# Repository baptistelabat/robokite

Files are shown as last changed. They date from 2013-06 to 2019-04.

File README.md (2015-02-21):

robokite
========

The robokite project aims to provide an open source platform to control kites.

This project started in 2013. It aims to provide tools or interface between existing tools to control big kites in a few years. Applications vary from ship propulsion to Airborne Wind Energy, through arstistic control.

Watch the video below to understand the current state of the project or have a look to the project blog http://robokite.blogspot.fr/

Joystick kite control (https://www.youtube.com/watch?v=0MbRyefYqPs&index=1&list=UUa67hFWRqXyehBhyk3YfBnA)

The first step is to design a simple kite control system:

* inexpensive
* adaptable to any small kite
* based on a community of users 

The solutions which are tested:
    
* Mobile phone (webcam, accelerometer, magnetometer, and gyro if available) for kite position sensing from ground
* Wifi streaming to a computer (might be raspberry) and processing with python (simplecv) in a first step
* Processing with OpenCV for Android then streaming to reduce latency, in a second step
* IMU embedded on kite with radio link to ground
* A webserver (python tornado)
* A browser with HTML5 as interface (websocket for real time, slider for controls, webgl for visualization, graphs, etc)
* A common gamepad joystick to send orders
* Serial NMEA or mavlink communication
* Arduino as a DAC (Digital-Analog Converter)
* Sabertooth as motor control card (to be replaced by open hardware)
* Recycled cordless drill as motor, but scalable.

Installation
------------

Please use the following command to get the code (you need to have git installed):

    git clone https://github.com/baptistelabat/robokite.git

This will create a repertory robokite containing the source code.

The following command will download the depencies (tests on ubuntu 14.04, work in progress):

    cd robokite
    chmod 777 install.sh
    ./install.sh

Feature status
--------------

Currently, the project enables to control the kite with some motors controlled by a joystick.

Documentation
--------------

The project hosts the documentation on the [wiki] (https://github.com/baptistelabat/robokite/wiki). Please use the following command to get the documentation offline:

    git clone https://github.com/baptistelabat/robokite.wiki.git

To get more up to date news, you can follow the [robokite blog](http://robokite.blogspot.fr/) 

Mailing list
------------

There is a public [mailing list](https://groups.google.com/group/robokite)
for Robokite users and developers.

Development
-----------

We are currently looking for some beta testers and developers.

Please mail nautilabs@gmail.com to be involved. 

Acknowledgments
------------

The robokite project is based on many open source or open hardware parts and was possible thanks to the support of several individuals and structures.

See [acknowlegement page in wiki] (https://github.com/baptistelabat/robokite/wiki/Acknowledgment).

License
-------

Robokite is covered by the MIT license, see the accompanying file LICENSE.md for details.

This repository contains additional code that may be covered by other licenses.

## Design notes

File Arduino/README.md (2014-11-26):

Arduino sketches
========

This directory host the arduino sketches.
Some are just some tests to checks sensors, actuators or communication links.

Simple: load this program on an arduino connected to a Sabertooth card controlling motors.
It receives order via NMEA messages on serial port. 
See motorJoy.py to generate orders from an USB joystick.

MPU9150_AHRS: this is the program to load on the arduino board connected to the IMU onboard kite.
It is making the data fusion of accelerometer, gyro and magnetometer
The software was found to work with MPU6050 alone and with MPU9050

Tests program
ArduinoMAVLink: this is a test to send fake attitude and gps data from arduino to ground control station with MAVLink

Electronic_rule: this is the program used to read measurement from the diy linear encoder.

Other sketches are obsolete

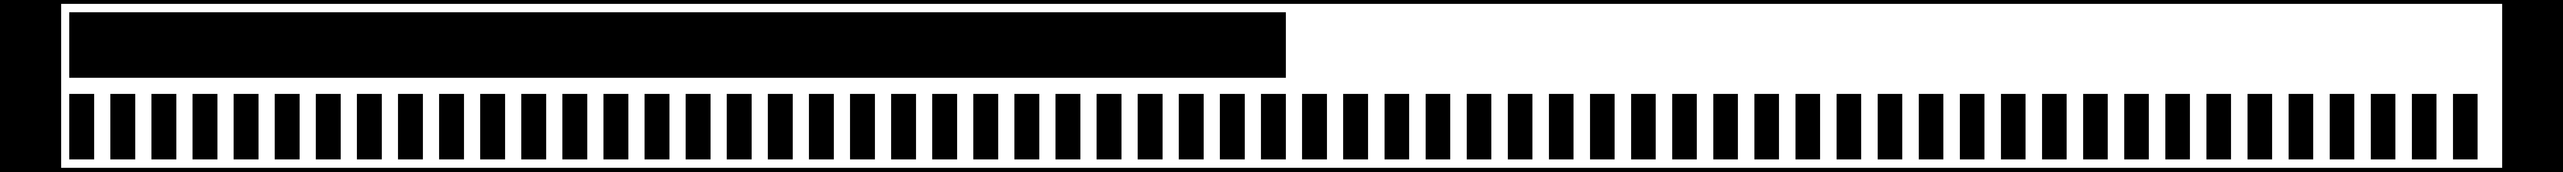
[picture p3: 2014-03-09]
Hardware/electronic_rule/sticker.png

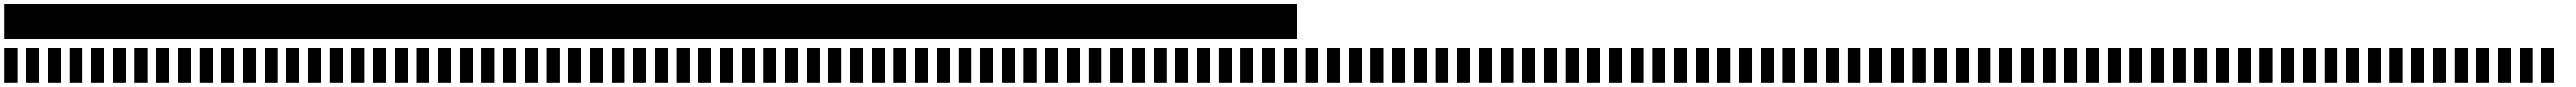
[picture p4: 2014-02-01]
Hardware/electronic_rule/stickerA3.png

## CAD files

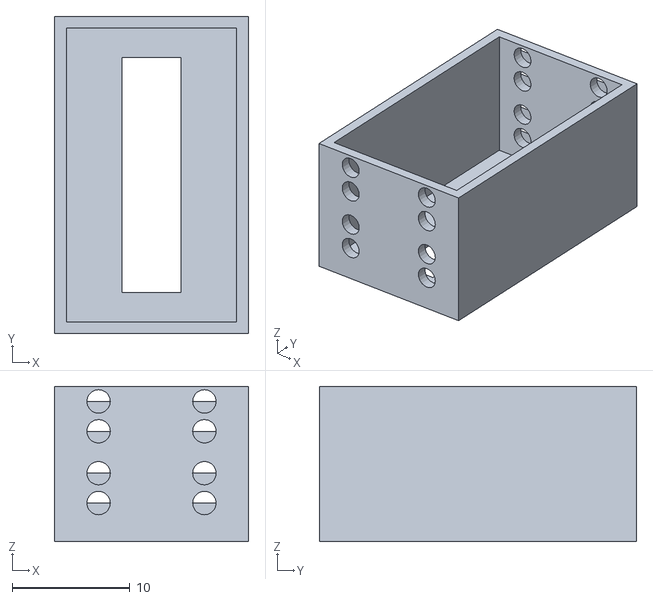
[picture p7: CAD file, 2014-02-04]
Hardware/electronic_rule/slider.stl
16.5 x 27.0 x 13.2

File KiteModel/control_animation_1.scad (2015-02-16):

distance_between_fixed_pulleys = 30;
distance_between_lines = 30;
control_length_left = 20 + 20*sin($t*360);
control_length_right = 20 + 20*sin($t*360*2);
L=300;


// Left line
hull()
{
translate([ -distance_between_lines,0,0]) sphere(r=1);
translate([ -control_length_left -distance_between_lines, distance_between_fixed_pulleys/2., 0]) sphere(r=1);
};
hull()
{
translate([ -control_length_left -distance_between_lines, distance_between_fixed_pulleys/2., 0]) sphere(r=1);
translate([ -distance_between_lines, distance_between_fixed_pulleys, 0]) sphere(r=1);
};
hull()
{
translate([ -distance_between_lines, distance_between_fixed_pulleys, 0]) sphere(r=1);
translate([ -distance_between_lines, distance_between_fixed_pulleys + 300 -2*sqrt(pow(distance_between_fixed_pulleys/2., 2)+ pow(control_length_left, 2)) , 0]) sphere(r=1);
};

// Central line
hull()
{
translate([ -0*distance_between_lines,0,0]) sphere(r=1);
translate([ -0*distance_between_lines, distance_between_fixed_pulleys, 0]) sphere(r=1);
};
hull()
{
translate([ -0*distance_between_lines, distance_between_fixed_pulleys, 0]) sphere(r=1);
translate([ -0*distance_between_lines, distance_between_fixed_pulleys + L -2*sqrt(pow(distance_between_fixed_pulleys/2., 2)) , 0]) sphere(r=1);
};

// Right line
hull()
{
translate([ distance_between_lines,0,0]) sphere(r=1);
translate([ control_length_right +distance_between_lines, distance_between_fixed_pulleys/2., 0]) sphere(r=1);
};
hull()
{
translate([ control_length_right +distance_between_lines, distance_between_fixed_pulleys/2., 0]) sphere(r=1);
translate([ distance_between_lines, distance_between_fixed_pulleys, 0]) sphere(r=1);
};
hull()
{
translate([ distance_between_lines, distance_between_fixed_pulleys, 0]) sphere(r=1);
translate([ distance_between_lines, distance_between_fixed_pulleys + 300 -2*sqrt(pow(distance_between_fixed_pulleys/2., 2)+ pow(control_length_right, 2)) , 0]) sphere(r=1);
};

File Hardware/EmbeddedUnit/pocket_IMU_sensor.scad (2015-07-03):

thickness = 2;
width=85;
length=133-30;
nano_length_max=43.6;
nano_length_min = 37.1;
nano_width_max = 22.7;
nano_internal_width = 9;
nano_thickness=7;
9V_width=26.2;
9V_length=45;
transmitter_width = 30;
transmitter_length= 45;
IMU_screw_spacing_width = 12.1;
IMU_screw_spacing_length = 16.3;
corner_radius=5;

module support()
{
	difference()
	{
		minkowski(){
		translate([0,-15,0]) cube(size=[width-2*corner_radius,length-2*corner_radius,thickness/3.], center=true);
		cylinder(h=thickness/3., r=corner_radius);
}
		translate([10,12,0]) difference(){
			cube(size=[nano_width_max,nano_length_min,2*thickness], center=true);
		 	cube(size=[nano_internal_width,nano_length_min,2*thickness], center=true);
	}
		translate([-23,8,0]) cube(size=[9V_width,9V_length,2*thickness], center=true);
		//translate([10,-45,0]) cube(size=[transmitter_length,transmitter_width,2*thickness], center=true);
	translate([0,-60,0]) cube(size=[12,3,2*thickness], center=true);
	translate([0,-60 +transmitter_width ,0]) cube(size=[12,3,2*thickness], center=true);
	
	
	// Holes to screw drotek IMU board	
		translate([-30, -50,0]) cylinder(r=0.3, h=2*thickness, center=true);
		translate([-30+IMU_screw_spacing_length, -50+IMU_screw_spacing_width,0]) cylinder(r=0.3, h=2*thickness, center=true);
		translate([-30+IMU_screw_spacing_length, -50,0]) cylinder(r=0.3, h=2*thickness, center=true);
	}
}
projection() support();

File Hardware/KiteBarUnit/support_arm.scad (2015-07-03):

use <compass.scad>
use <arduino_footprint.scad>
use <battery_footprint.scad>


module support_arm()
{
	thickness = 5;
	
	difference()
	{
		union()
		{
			arm();
			minkowski()
			{
				cylinder(r=5, h=thickness/3.0);
				translate([20,0,0]) cube(size=[50,150,thickness/3.0], center=true);
			}		
		}
		translate([20,-45,0]) nano_connector_footprint(2*thickness);
		translate([20,5,0]) 9V_battery();
		translate([0,5,0]) cube(size=[3,12,2*thickness], center=true);
		translate([40,5,0]) cube(size=[3,12,2*thickness], center=true);
		translate([0,-45,0]) cube(size=[3,12,2*thickness], center=true);
		translate([40,-45,0]) cube(size=[3,12,2*thickness], center=true);
	}
}
projection() support_arm();

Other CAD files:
Hardware/RingEncoder/ring_encoder.scad
Hardware/GroundStation/ground_station.scad
Hardware/KiteBarUnit/bar_mount_reduced.scad
Hardware/KiteBarUnit/compass.scad
Hardware/KiteBarUnit/gimbal_connection.scad
Hardware/KiteBarUnit/line_support.scad
Hardware/KiteBarUnit/potentiometer_support.scad
Hardware/KiteBarUnit/ring.scad
Hardware/Obsolete/MobileSupport/mobile_support.scad
Hardware/Obsolete/bar_mount.scad
Hardware/Obsolete/embedded_support.scad
Hardware/Obsolete/line_tension_measurement support.scad
Hardware/Obsolete/tender.scad
Hardware/arduino_footprint.scad
Hardware/bar_mount.scad
Hardware/battery_footprint.scad
Hardware/electronic_rule/slider.scad
Hardware/embedded_support.scad
Hardware/handle.scad
Hardware/line_tension_measurement support.scad
Hardware/mobile_support.scad
Hardware/tender.scad
kite.scad

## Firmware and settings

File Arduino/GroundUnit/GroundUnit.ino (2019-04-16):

// Copyright (c) 2013 Nautilabs
// https://github.com/baptistelabat/robokite

// This file used SoftwareSerial example (Copyright (c) 2012 Dimension Engineering LLC)
// for Sabertooth http://www.dimensionengineering.com/software/SabertoothSimplifiedArduinoLibrary/html/index.html
// See license.txt in the Sabertooth arduino library for license details.
//
// The Sabertooth selector 1 3 5 6 have to be on on.

// Includes
#include <SoftwareSerial.h> 
#include <SabertoothSimplified.h> // From http://www.dimensionengineering.com/software/SabertoothArduinoLibraries.zip
#include <TinyGPS++.h>    // From https://github.com/mikalhart/TinyGPSPlus
#include <PID_v1.h>       // From https://github.com/br3ttb/Arduino-PID-Library/tree/master/PID_v1
#include <SPI.h> // Not actualy used but needed to compile
#include <MavlinkForArduino.h>

// Port definition
#define      TX_PIN 8 // Plug to Sabertooth RX
#define      RX_PIN 10 // Do not plug
#define RF_DATA_PIN 11
#define     LED_PIN 13 // Built-in led


// String management
String inputString = "";         // a string to hold incoming data
boolean stringComplete = false;  // whether the string is complete

// Sabertooth connection
// Note: NOT_A_PIN (0) was previously used for RX which is not used, but this was causing problems
SoftwareSerial SWSerial(RX_PIN, TX_PIN); // RX, TX. RX on no pin (unused), TX on pin 8 (to S1).
SabertoothSimplified ST(SWSerial); // Use SWSerial as the serial port.
int power1, power2;

// NMEA protocol for robust messages
TinyGPSPlus nmea;
// O stands for Opensource, R for Robokite
// The index is the place of the field in the NMEA message
TinyGPSCustom feedback_request      (nmea, "ORFBR", 1);  // Feedback request. The feedback are normalized between 0 and 1023
// The orders are normalized between -127 and 127
TinyGPSCustom pwm1     (nmea, "ORPW1", 1);  // Dimentionless voltage setpoint (Pulse Width Modulation) for Sabertooth output 1
TinyGPSCustom pwm2     (nmea, "ORPW2", 1);  // Dimentionless voltage setpoint (Pulse Width Modulation) for Sabertooth output 2
TinyGPSCustom setpos1  (nmea, "ORSP1", 1);  // Position setpoint for Sabertooth output 1
TinyGPSCustom setpos2  (nmea, "ORSP2", 1);  // Position setpoint for Sabertooth output 2
TinyGPSCustom speedlim1  (nmea, "ORSL1", 1);  // Speed limitation for Sabertooth output 1
TinyGPSCustom speedlim2  (nmea, "ORSL2", 1);  // Speed limitation for Sabertooth output 2
TinyGPSCustom poslim1  (nmea, "ORPL1", 1);  // Position limitation for Sabertooth output 1
TinyGPSCustom poslim2  (nmea, "ORPL2", 1);  // Position limitation for Sabertooth output 2
TinyGPSCustom kpm1 (nmea, "ORKP1", 1); // Proportional coefficient multiplicator
//TinyGPSCustom kim1 (nmea, "ORKI1", 1); // Integral coefficient multiplicator
TinyGPSCustom kdm1 (nmea, "ORKD1", 1); // Derivative coefficient multiplicator
//TinyGPSCustom kpm2 (nmea, "ORKP2", 1); // Proportional coefficient multiplicator
//TinyGPSCustom kim2 (nmea, "ORKI2", 1); // Integral coefficient multiplicator
//TinyGPSCustom kdm2 (nmea, "ORKD2", 1); // Derivative coefficient multiplicator
boolean isFeedbackRequested = false;

uint8_t data[4];  // 2 element array of unsigned 8-bit type, holding Joystick readings



// PID for robust control
// Define Variables we'll be connecting to
double Setpoint1, Input1, Output1;
double Setpoint2, Input2, Output2;
double Input3, Input4, Input5, Input6;
float posSat1 = 1;
float posSat2 = 1;
float speedSat1 = 1;
float speedSat2 = 1;
// Specify the links and initial tuning parameters (Kp, Ki, Kd)
float Kp1 = 1;
float Ki1 = 0.00;
float Kd1 = 0.001;
float Kp2 = 1;
float Ki2 = 0.00;
float Kd2 = 0.001;
PID myPID1(&Input1, &Output1, &Setpoint1, Kp1, Ki1, Kd1, DIRECT);
PID myPID2(&Input2, &Output2, &Setpoint2, Kp2, Ki2, Kd2, DIRECT);


#define ORDER_RATE_ms 100
long last_order_ms = 0;
long last_simu_ms = 0;
int dt_ms = 0;

boolean SIL = false; // Use Software in the Loop simulation

/* HX711 part */
#include "HX711.h"

#define HX711_DOUT  12 // or DAT
#define HX711_CLK   11
#define HX711_GND   13

#define OFFSET -797000 // From raw value when no load
#define SCALE  37.0  // From calibration
HX711 scale;
long raw_value;
void setup()
{
  setupHX711();
  pinMode(LED_PIN, OUTPUT); 
  
  // Initialize software serial communication with Sabertooth 
  SWSerial.begin(9600);
  
  // Initialize serial communications with computer
  Serial.begin(115200);
  
  // Reserve bytes for the inputString:
  inputString.reserve(200);
  
  // Initialize input and setpoint
  Input1 = 0;
  Input2 = 0;
  Input3 = 0;

  Setpoint1 = 0;
  Setpoint2 = 0;
  
  // Turn the PID on
  myPID1.SetMode(MANUAL);
  myPID2.SetMode(MANUAL);
  // Saturate the output to the maximum range (values are normalized between -1 and 1)
  myPID1.SetOutputLimits(-1, 1);
  myPID2.SetOutputLimits(-1, 1);
  
  for (int i=0;i<4;i++)
  {
    data[i] = 127;
  }
  
  last_simu_ms = millis();
}

void setupHX711() {
  // Ground connection
  scale.begin(HX711_DOUT, HX711_CLK);
  pinMode(HX711_GND, OUTPUT);
  Serial.print("HX711_DOUT -> D");
  Serial.println(HX711_DOUT);
  Serial.print("HX711_CLK -> D");
  Serial.println(HX711_CLK);
  Serial.print("HX711_GND -> D");
  Serial.println(HX711_GND);
  Serial.println("HX711_VCC -> 3V3");

   // No calibration, read the raw value
  scale.set_offset(0);
  scale.set_scale(1);
}

/*
  SerialEvent occurs whenever a new data comes in the
 hardware serial RX.  This routine is run between each
 time loop() runs, so using delay inside loop can delay
 response.  Multiple bytes of data may be available.
 */
void serialEvent()
{
  while (Serial.available()) {
    // Get the new byte:
    char inChar = (char)Serial.read(); 
    // Add it to the inputString:
    inputString += inChar;
    // If the incoming character is a newline, set a flag
    // so the main loop can do something about it:
    if (inChar == '\n') {
      stringComplete = true;
    } 
  }
}

void loop()
{
   processSerialInput();
   processInput();
   if (false==SIL)
   {
     computeFeedback();
   }
   computeOrder();
   sendOrder();
   if (SIL)
   {
     simulate();
   }
   sendFeedback();
   delay(10);
}
void processInput()
{
  data[0] = scale.get_units();
  Input1 = (data[0]-OFFSET)/SCALE;


  Input4 = analogRead(A0)/1023.;
  Input5 = analogRead(A1)/1023.;
  Input6 = analogRead(A2)/1023.;
}

void processSerialInput()
{
  // Print the string when a newline arrives:
  if (stringComplete)
  {   
    // Serial.println(inputString);
    char ctab[inputString.length()+1];
    inputString.toCharArray(ctab, sizeof(ctab));
    char *gpsStream = ctab;

    while (*gpsStream)
    {
      if (nmea.encode(*gpsStream++))
      {
        if (pwm1.isUpdated())
        { 
          pwm1.value();
          myPID1.SetMode(MANUAL);
        }
        if (pwm2.isUpdated())
        {
          pwm2.value();
          myPID2.SetMode(MANUAL);
        }
        if (setpos1.isUpdated())
        { 
          setpos1.value();
          myPID1.SetMode(AUTOMATIC);
        }
        if (setpos2.isUpdated())
        {
          setpos2.value();
          myPID2.SetMode(AUTOMATIC);
        }
        if (feedback_request.isUpdated())
        {
          feedback_request.value();
          // $ORFBR,0*57
          isFeedbackRequested = true;
          digitalWrite(LED_PIN, HIGH);
        }
        if (kpm1.isUpdated()||kdm1.isUpdated())//||kpm2.isUpdated()||kim2.isUpdated()||kdm2.isUpdated())
        {
          kpm1.value();
          kdm1.value();
          computePIDTuning();
        }
        if (speedlim1.isUpdated()||speedlim2.isUpdated()||poslim1.isUpdated()||poslim2.isUpdated())
        {
          updateSaturation();
          speedlim1.value();
          speedlim2.value();
          poslim1.value();
          poslim2.value();
        }  
      }
    }
    // Clear the string:
    inputString = "";
    stringComplete = false;
  }
}

void computeFeedback()
{
  
  // Feedbacks are normalized between -1 and 1
  
  // Potentiometer angle
  float rawAngle_deg = (data[0]-127)/255.0;
  
}

void sendFeedback()
{
  /*mavlink_message_t msg; 
  uint8_t bufout[MAVLINK_MAX_PACKET_LEN];
  uint16_t len;
  uint64_t time_us = micros();
  int group_mlx = 0;
  uint8_t system_id = 100;
  uint8_t target_system = system_id;
  uint8_t component_id = 1;
  uint8_t target_component = 2;// Sabertooth
  */
  // All the feedback values are normalized in the range 0-1023 (10 bits resolution)
  if (isFeedbackRequested)
  {
    
    float orders[8];
    orders[0] = float(power1/127.);
    orders[1] = float(power2/127.);
    //mavlink_msg_set_actuator_control_target_pack(system_id, component_id, &msg, time_us, group_mlx, target_system, target_component, orders);
    //len = mavlink_msg_to_send_buffer(bufout, &msg);
    //Serial.write(bufout, len);
    
    Serial.print((power1+127)*4);
    Serial.print(", ");
    Serial.print((power2+127)*4);
    Serial.print(", ");
    Serial.print((Input1+1)/2.*1023);
    Serial.print(", ");
    Serial.print((Input2+1)/2.*1023);
    Serial.print(", ");
    Serial.print((Input3+1)/2.*1023);
    Serial.print(", ");
    Serial.print((Input4+1)/2.*1023);
    Serial.print(", ");
    Serial.print((Input5+1)/2.*1023);
    Serial.print(", ");
    Serial.print((Input6+1)/2.*1023);
    Serial.println("");
    isFeedbackRequested = false;
  }
}

void computeOrder()
{
  if (myPID1.GetMode() == MANUAL)
  {
    power1 = atoi(pwm1.value())*speedSat1;
  }
  if (myPID2.GetMode() == MANUAL)
  {
    power2 = atoi(pwm2.value())*speedSat2;
  }
  if (myPID1.GetMode() == AUTOMATIC)
  {
    Setpoint1 = atoi(setpos1.value())/127.*posSat1*1.3;//Factor to go a bit further and be sure to reach saturation (even with static error)
    myPID1.Compute();
    power1 = Output1*127;
  }
  if (myPID2.GetMode() == AUTOMATIC)
  {
    Setpoint2 = atoi(setpos2.value())/127.*posSat2*1.3;
    myPID2.Compute();
    power2 = Output2*127;
  }
  if (Input1>posSat1)
  {
    power1 = min(power1,0);
  }
  if (Input1<-posSat1)
  {
    power1 = max(power1,0);
  }
}

void sendOrder()
{
  if (fabs(millis()-last_order_ms)>ORDER_RATE_ms)
  {
    last_order_ms = millis();
  // Order in the range -127/127
    //SWSerial.println(127);
      //Saturation based on posSat
   ST.motor(1, power1);
   ST.motor(2, power2);
  }
}
void computePIDTuning()
{
   myPID1.SetTunings(fabs(atof(kpm1.value())/127.*Kp1), 0, fabs(atof(kdm1.value())/127.*Kd1));
 
 //myPID1.SetTunings(fabs(atof(kpm1.value())/127.*Kp1), fabs(atof(kim1.value())/127.*Ki1), fabs(atof(kdm1.value())/127.*Kd1));
 //myPID2.SetTunings(fabs(atof(kpm2.value())/127.*Kp2), fabs(atof(kim2.value())/127.*Ki2), fabs(atof(kdm2.value())/127.*Kd2));
 myPID1.SetControllerDirection(sgn(atoi(kpm1.value())));
 //myPID2.SetControllerDirection(sgn(atoi(kpm2.value())));
 //Serial.println(atof(kpm1.value())/127.*Kp1);
}
void updateSaturation()
{
  if (speedlim1.isUpdated())
  {
     myPID1.SetOutputLimits(-atoi(speedlim1.value())/127., atoi(speedlim1.value())/127.);
     speedSat1 = atoi(speedlim1.value())/127.;
  }
  if (speedlim2.isUpdated())
  {
    myPID2.SetOutputLimits(-atoi(speedlim2.value())/127., atoi(speedlim2.value())/127.);
  }
  if (poslim1.isUpdated())
  {
    posSat1 = atoi(poslim1.value())/127.;
  }
  //posSat2 = atoi(poslim2.value())/127.;
}
static inline int8_t sgn(int val) {
  if (val < 0) return -1;
  if (val==0) return 0;
  return 1;
}
 
void simulate()
{ dt_ms = millis()-last_simu_ms;
  Input1=Input1+power1/127.*dt_ms/1000.;
  Input2=Input2+power2/127.*dt_ms/1000.;
  last_simu_ms= millis();
}

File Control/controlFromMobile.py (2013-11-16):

#!/usr/bin/env python
# -*- coding: utf8 -*-
#
# Copyright (c) 2013 Nautilabs
#
# Licensed under the MIT License,
# https://github.com/baptistelabat/robokite
# Authors: Baptiste LABAT, 
#
# This script is used as a gateway between a mobile phone and an arduino commanding a motor
# The mobile phone sensors can then be used to control the motor
#
# The sensors data are streamed over wifi by sensorUDP application on android mobile phone.
# The UDP packet are read by the python script then forwarded
import os
import sys
import threading
import time
import numpy as np
import serial
sys.path.append(os.getcwd())
sys.path.append('../Sensors')
import mobileState

def computeXORChecksum(chksumdata):
	# Inspired from http://doschman.blogspot.fr/2013/01/calculating-nmea-sentence-checksums.html
    # Initializing XOR counter
    csum = 0
    
    # For each char in chksumdata, XOR against the previous 
    # XOR char.  The final XOR of the last char will be the
    # checksum  
    for c in chksumdata:
        # Makes XOR value of counter with the next char in line
        # and stores the new XOR value in csum
        csum ^= ord(c)
    h = hex(csum)    
    return h[2:]#get hex data without 0x prefix
    
    
try:
  # Get the mobile orientation
  mobile = mobileState.mobileState()
  a = threading.Thread(None, mobileState.mobileState.checkUpdate, None, (mobile,))
  a.start()

  # Open the serial port
  locations=['/dev/ttyACM0','/dev/ttyACM1','/dev/ttyACM2','/dev/ttyUSB0','/dev/ttyUSB1','/dev/ttyUSB2','/dev/ttyUSB3','/dev/ttyS0','/  dev/ttyS1','/dev/ttyS2','/dev/ttyS3']
  for device in locations:
    try:
      print "Trying...",device
      ser = serial.Serial(
	port = device,
	baudrate = 9600
	)
      break
    except:
      print "Failed to connect on",device
  time.sleep(1.5) # Arduino is reset when opening port so wait before communicating
  ser.flush()
  ser.write('i1')
  dt = 0.1
  while True:
      mobile.computeRPY()
      ser.flush()
      alpha = np.max([-0.99, np.min([0.99, np.floor(100*mobile.pitch/2.0)/100.0])]
                          )
      msg = "ORPWM"+","+str(alpha)
      msg = "$"+msg +"*"+ computeXORChecksum(msg) + chr(13).encode('ascii')
      ser.write(msg
        )
      print msg
      time.sleep(dt)
except KeyboardInterrupt:
 mobile.stop_requested = True

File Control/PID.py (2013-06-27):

class PID:
    def __init__(self, Kp=1, Ki=0.1, Kd=1, maxIntegralCorrection=0, minIntegralCorrection=-0):
        self.Kp = Kp # Proportional gain
        self.Ki = Ki # Integral gain
        self.Kd = Kd # Derivative gain
        self.integral = 0
	self.maxOutput = 1
	self.minOutput = -1
    def incrementTime(self, error, dt):
        self.integral = self.integral + error*self.Ki*dt
    def computeCorrection(self, error, derror):
        correction = self.Kp*(error) + self.Kd*derror + self.integral
        correction = min(max(correction, self.minOutput), self.maxOutput)
        return correction

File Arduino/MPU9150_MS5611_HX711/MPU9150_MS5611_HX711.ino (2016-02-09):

/*****************************************************************
MPU9150_AHRS_directdata.ino
SFE_MPU9150 Library AHRS Data Fusion Example Code
Kris Winer for Sparkfun Electronics
Original Creation Date: April 8, 2014
https://github.com/sparkfun/MPU9150_Breakout

The MPU9150 is a versatile 9DOF sensor. It has a built-in
accelerometer, gyroscope, and magnetometer that
functions over I2C. It is very similar to the 6 DoF MPU6050 for which an extensive library has already been built.
Most of the function of the MPU9150 can utilize the MPU6050 library.

This Arduino sketch utilizes Jeff Rowberg's MPU6050 library to generate the basic sensor data
for use in two sensor fusion algorithms becoming increasingly popular with DIY quadcopter and robotics engineers. 
I have added and slightly modified Jeff's library here.

This simple sketch will demo the following:
* How to create a MPU6050 object, using a constructor (global variables section).
* How to use the initialize() function of the MPU6050 class.
* How to read the gyroscope, accelerometer, and magnetometer
  using the readAcceleration(), readRotation(), and readMag() functions and the
  gx, gy, gz, ax, ay, az, mx, my, and mz variables.
* How to calculate actual acceleration, rotation speed, magnetic
  field strength using the  specified ranges as described in the data sheet:
  http://dlnmh9ip6v2uc.cloudfront.net/datasheets/Sensors/IMU/PS-MPU-9150A.pdf
  and
  http://dlnmh9ip6v2uc.cloudfront.net/datasheets/Sensors/IMU/RM-MPU-9150A-00.pdf.
  
In addition, the sketch will demo:
* How to check for data updates using the data ready status register
* How to display output at a rate different from the sensor data update and fusion filter update rates
* How to specify the accelerometer and gyro sampling and bandwidth rates
* How to use the data from the MPU9150 to fuse the sensor data into a quaternion representation of the sensor frame
  orientation relative to a fixed Earth frame providing absolute orientation information for subsequent use.
* An example of how to use the quaternion data to generate standard aircraft orientation data in the form of
  Tait-Bryan angles representing the sensor yaw, pitch, and roll angles suitable for any vehicle stablization control application.

Hardware setup: This library supports communicating with the
MPU9150 over I2C. These are the only connections that need to be made:
	MPU9150 --------- Arduino
	 SCL ---------- SCL (A5 on older 'Duinos')
	 SDA ---------- SDA (A4 on older 'Duinos')
	 VDD ------------- 3.3V
	 GND ------------- GND

The LSM9DS0 has a maximum voltage of 3.5V. Make sure you power it
off the 3.3V rail! And either use level shifters between SCL
and SDA or just use a 3.3V Arduino Pro.	  

Development environment specifics:
	IDE: Arduino 1.0.5
	Hardware Platform: Arduino Pro 3.3V/8MHz
	MPU9150 Breakout Version: 1.0

This code is beerware. If you see me (or any other SparkFun 
employee) at the local, and you've found our code helpful, please 
buy us a round!

Distributed as-is; no warranty is given.
*****************************************************************/
/*
MS561101BA_altitude.pde - Computes altitude from sea level using pressure readings from the sensor.
The algorithm uses the Hypsometric formula as explained in http://keisan.casio.com/has10/SpecExec.cgi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

Copyright (C) 2011 Fabio Varesano <fvaresano@yahoo.it>

Development of this code has been supported by the Department of Computer Science,
Universita' degli Studi di Torino, Italy within the Piemonte Project
http://www.piemonte.di.unito.it/


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
*/

#define USE_MAVLINK //Uncomment this line to use mavlink
#ifdef USE_MAVLINK
  #include "MavlinkForArduino.h"        // Mavlink interface
#endif

#include <Wire.h>
#include "I2Cdev.h" //from https://github.com/sparkfun/MPU-9150_Breakout.git
#include "MPU6050_9Axis_MotionApps41.h"
#include <MS561101BA.h>

#define OUTPUT_RATE_ms 50 // 20Hz

#define MOVAVG_SIZE 32

// Define corrections/offsets for magnetometer
#define LOCAL_DECLINATION_DEG -3 //at Nantes, France is around 3 degrees in 2014
#define MAG_1_OFFSET -7.0f
#define MAG_2_OFFSET 75.0f
#define MAG_3_OFFSET 117.0f
#define ACC_1_OFFSET 0.0f
#define ACC_2_OFFSET 0.0f
#define ACC_3_OFFSET 0.0f
#define GYRO_1_OFFSET -284.8f
#define GYRO_2_OFFSET -161.0f
#define GYRO_3_OFFSET 12.7f
#define GYRO_RANGE_DEGPS 250.0f
#define ACCEL_RANGE_G 2.0f
#define MAG_RANGE_mG 12290.0f// milliGauss (1229 microTesla per 2^12 bits, 10 mG per microTesla)

// class default I2C address is 0x68
// specific I2C addresses may be passed as a parameter here
// AD0 low = 0x68 (default for InvenSense evaluation board)
// AD0 high = 0x69
MPU6050 accelGyroMag(0x69);

// global constants for 9 DoF fusion and AHRS (Attitude and Heading Reference System)
#define GyroMeasError PI * (40.0f / 180.0f)       // gyroscope measurement error in rads/s (shown as 3 deg/s)
#define GyroMeasDrift PI * (0.0f / 180.0f)      // gyroscope measurement drift in rad/s/s (shown as 0.0 deg/s/s)
// There is a tradeoff in the beta parameter between accuracy and response speed.
// In the original Madgwick study, beta of 0.041 (corresponding to GyroMeasError of 2.7 degrees/s) was found to give optimal accuracy.
// However, with this value, the LSM9SD0 response time is about 10 seconds to a stable initial quaternion.
// Subsequent changes also require a longish lag time to a stable output, not fast enough for a quadcopter or robot car!
// By increasing beta (GyroMeasError) by about a factor of fifteen, the response time constant is reduced to ~2 sec
// I haven't noticed any reduction in solution accuracy. This is essentially the I coefficient in a PID control sense; 
// the bigger the feedback coefficient, the faster the solution converges, usually at the expense of accuracy. 
// In any case, this is the free parameter in the Madgwick filtering and fusion scheme.
#define beta sqrt(3.0f / 4.0f) * GyroMeasError   // compute beta
#define zeta sqrt(3.0f / 4.0f) * GyroMeasDrift   // compute zeta, the other free parameter in the Madgwick scheme usually set to a small or zero value
#define Kp 2.0f * 5.0f // these are the free parameters in the Mahony filter and fusion scheme, Kp for proportional feedback, Ki for integral
#define Ki 0.0f

#define RAW       0
#define FUSION    1
#define DEBUG     2
short outputMode = FUSION;

// String management
String inputString = "";         // a string to hold incoming data
boolean stringComplete = false;  // whether the string is complete


int16_t a1, a2, a3, g1, g2, g3, m1, m2, m3;     // raw data arrays reading
uint16_t last_output_ms = 0;  // used to control display output rate
uint16_t delt_t_ms = 0; // used to control display output rate
uint8_t BaroRate;     // read rate for magnetometer data
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

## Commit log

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2013-04-03 Add a script to make the selection of the object to track and to check the corresponding histogram
2013-05-17 Add a simple PID library (to be replaced by existing one)
    [PID.py]
2013-06-16 Correct typing error and arrange indentation
    [PID.py]
2013-06-20 Add several comments Automatically adapts display size to video Change variable name from updateSelection to selectionInProgress Add a parameter (hard coded) not to use orientation messages Add a try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
    [simpleTrack.py]
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2013-06-22 increase the width to avoid problem with aliasing
    [simpleTrack.py]
2013-06-24 Introduce threading to be able to filter data and reduce waiting time
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2013-06-26 Correct indentation error (useless loop)
    [simpleTrack.py]
2013-06-26 Correct a bug (localProjection reference is the middle of the screen)
    [simpleTrack.py]
2013-06-26 Correct an error between degrees and radians (unwrap was not done)
    [simpleTrack.py]
2013-06-26 Suppress the possibility to rotate the image before processing : it is a bad idea because -takes computation time to rotate -the image is increased with black parts -which increase the computation ti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
    [simpleTrack.py]
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2013-06-27 Correct rotation to display grid if camera is rolled Create the function track
    [simpleTrack.py]
2013-06-27 Improve filter if missing data Output rate of turn Add a PID control output in the example
    [simpleTrack.py]
2013-06-27 Loop instead of waiting, (to solve problems of input message which were not received).
    [HBridgePWM.ino]
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2013-06-28 Add a frequency for the motor to stop if no more orders are received
2013-06-28 Try to improve detection when kite is on ground Not very effective Correct the computation of ROT based on elapsedTime
    [simpleTrack.py]
2013-06-28 Add the possibility to check if the kite angle is inverted and to correct for it
    [simpleTrack.py]
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2013-07-24 Flush hdf5 file to avoid getting a corrupted file if the program bug
    [simpleTrack.py]
2013-07-26 Add proof of concept of the use of Web socket -to react to modification by user -to display information Add sliders
2013-07-26 Add a test to check if an optical mouse can be used as a course sensor
2013-07-28 Fisrt version of a 3D model
    [kite.scad]
2013-07-28 Add animation in figure of 8
    [kite.scad]
2013-07-28 Change the shape of kite Change line length
    [kite.scad]
2013-07-31 Restructure Suppress dependency to PID library Use an image as bacground and as kite
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2013-08-06 Add a script to be able to control the motor based on mobile phone inclination. This can be used to control the kite while launching it if alone
2013-08-07 Move script. js according to Tornado example architecture Add control of motor through web interface
2013-08-09 try different serial port when opening connection Sent only valid command to avoid rejection.
    [controlFromMobile.py]
2013-08-09 Modification to avoid blocking state due to buffer saturation!
    [Sabertooth.ino]
2013-08-18 Intent to flush input buffer to avoid blocking write in arduino when buffer is full
    [server.py]
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2013-08-21 Add header Silence hdf5 error
    [simpleTrack.py]
2013-10-07 Add a flush to avoid delay when relaunching server
    [Sabertooth.ino]
2013-10-08 Suppress semi-column which was making a regression (motor not stopping when connection closed)
2013-10-16 Version with PID included. Bug after a few seconds...
    [Sabertooth.ino]
2013-10-19 The scheduler was commented which might explain many serial problems in past months!
    [server.py]
2013-10-24 Add debug information Correct a bug (close function does not exist it is on_close in tornado)
    [server.py]
2013-10-24 Use microseconds function instead of milliseconds, and add random to try to broad noise bandwith
    [HBridgePWM.ino]
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2013-10-24 Solve serial connection problem by increasing the frequency at which serial data are read, which enable the arduino not to block
2013-10-24 Use serial instead of arduino serial. Increase the checksertial frequency to avoid arduino buffer overflow. Was tested with success during more than 10 minutes.
    [server.py]
2013-10-27 Complete rework of the man machine interface
    [server.py]
2013-10-28 Update to be able to control 2 motors. Tested during 20 minutes
2013-11-04 Add the possibility to get raw or filtered data. Save the data to text file for calibration
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2013-11-05 Add possibility to have 0 time filter constant Add possibility to change order of axes of reference Add another algorithm to find orientation (finally not as good)
2013-11-05 Add observation vectors representation (magnetic, acceleration) Correct the euler order convention Possibility to use quaternion Draw with z up.
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2013-11-10 Do not use Firmata (too slow) Plots severl pins data
    [server.py]
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2013-11-11 Test the tracking of RED and WHITE blinking led in night (filtering and rejection to be improved)
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2013-11-15 Add comments Add default behaviour Improve behaviour in case of failure
    [benchPythonArduino.py]
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2014-01-22 Intermediate files till gcode
    [support.dxf]
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2014-01-24 The code which was used to cut. There were some problems due to the circles which are converted into many small segments
2014-01-26 Replace circle by small points (gcode to be modified manually)
    [support.dxf]
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2014-02-04 Add slider design (scad was used not ko)
    [slider.scad, slider.stl]
2014-02-10 Work in progress: -add output for debug -correct syntax -use external interrupts -rename pin
2014-03-13 Correct error at compilation (full object was taken instead of value field)
    [src.ino]
2014-03-13 Use SI units, add correction of position based on potentiometer reading
    [src.ino]
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2014-03-18 Correct an error due to missing leading zero which are expected for nmea messages
    [motorJoy.py, server.py]
2014-03-19 Correct small bug in xor checksum Replace tab with space Sort the import and deal with missing optional dependency
    [simpleTrack.py]
2014-03-19 Correct a bug at source in code (rgb) and save and reload image to correct an unknown problem which appears
    [simpleTrack.py]
2014-03-19 Use resize instead of scale, but does not really solve the problem
    [simpleTrack.py]
2014-03-26 Correct a bug due to bad indentation. Still a bug if button pressed before joystick use
    [motorJoy.py]
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2014-06-24 Commit example from https://launchpad.net/hmc58x3 Does not work on drotek imu 10dof http://www.drotek.fr/shop/fr/home/62-imu-10dof-mpu6050-hmc5883l-ms5611.html
    [HMC5883L_raw.ino]
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2014-07-15 Correct to be able to compile. However sketch is too big to be loaded
    [Attitude_Altitude.ino]
2014-07-16 Correct a bug (variable could be not initialized)
    [motorJoy.py]
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2014-07-29 Magnetometer calibration Read magnetometer and update filter at each interrupt (more often) to update correctly filter Add comments about plugging This version works nicely !
    [IMU_9DOF.ino]
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2014-11-23 Initial commit from https://github.com/sparkfun/MPU-9150_Breakout/tree/master/firmware/MPU6050/Examples (reverted from commit 525d000b9db36b64654d36508627fcc4dbb113e8)
    [Attitude_Altitude.ino, MPU9150_AHRS.ino, MPU9150_MS5611_IMU.ino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]
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2014-11-26 Replace video by chain
2014-11-27 No new functionalities but restructure the code, clear dead code, add comments, and correct the bug which appeared on newer arduino version
    [src.ino]
2014-11-27 Make a few correction so that the mode does not change from AUTO to MANUAL in case of joystick automatic reconnection (every 2 seconds!)
    [motorJoy.py]
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2014-11-29 Correct deg to rad conversion on offset correction Change motor sign to adapt to mechanical set up
    [src.ino]
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2014-11-29 Add serialEvent function to unfill buffer and avoid stopping program
    [MPU9150_AHRS.ino]
2014-11-29 Redefine modes Correct bugs Add trim
    [motorJoy.py]
2014-11-29 Correct a bug on offset in auto
    [motorJoy.py]
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2015-01-24 Add multiple comments Correct normalisations Get rid of 3.14 (pi) with a #define
    [src.ino]
2015-01-24 Improve comments and typo Get read of "dead code" Correct a bug when reseting trim in auto
    [motorJoy.py]
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2015-01-28 Use python3 compliant syntax (but pygame last version not working yet on python3)
    [motorJoy.py]
2015-01-28 Correct format as it do not correspond to the result of launching Recording/Videos/downloadTestVideos.sh
    [simpleTrack.py]
2015-01-28 Adding automatic download of video. Correcting its name after download
    [nightTrack.py]
2015-01-28 isUpToDate was never reset
    [mobileState.py]
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2015-02-06 Correct indentation error (tab instead of space)
    [motorJoy.py]
2015-02-06 Add offset on raw sensors measurements for calibration Correct measurement sign to fit with NED convention (connector being in -x direction)
    [MPU9150_MS5611_IMU.ino]
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2015-02-06 Change long to uint32_t (seems to reduce bug)
    [MPU9150_MS5611_IMU.ino]
2015-02-07 Get rid of hard coded values Increase the magnetometer reading frequency to reduce noise
    [MPU9150_MS5611_IMU.ino]
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2015-02-07 Rename the offset to avoid mixing number and axes (the magnetometer sensor does not have the same convention as accelerometer and gyro) Correct the update rate for magnetometer Save my own offsets!
    [MPU9150_MS5611_IMU.ino]
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2015-02-09 Reduce frequency from 100Hz to 20 Hz to avoid freezing observed on raspberry pi target.
    [motorJoy.py]
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2015-02-10 Use openscad to replace kokopelli piece to be more standard
    [mobile_support.scad]
2015-02-10 Ready to laser cut...
    [mobile_support.scad]
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2015-02-13 Add a deadband on power/depower axis to avoid changing setting when trying to change only steering, but to allow steering with and power/depower with only one joystick (one finger)
    [motorJoy.py]
2015-02-13 Save the work in progress: support for the line tension measurement unit
    [line_tension_measurement support.scad]
2015-02-16 Add an animation
    [control_animation_1.scad]
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2015-02-20 Compute ground pressure at initialisation to be able to get altitude relative to ground (for short time) Send the pressure in mavlink messages
    [MPU9150_MS5611_IMU.ino]
2015-02-20 Add some pieces to attach to the lines
    [mobile_support.scad]
2015-02-21 Create module and try to get projection Reduce resolution to get circles instead of polygons
    [mobile_support.scad]
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2015-02-21 Increase resolution to get less segments...
    [mobile_support.scad]
2015-02-21 dxf generated from openscad svg created from dxf, includes modification in layers gcode generated with laserengraver from svg (with default config of laserengraver)
    [support.dxf]
2015-02-21 Add a script for line tension measurement unit
    [line_tension_measurement support.scad]
2015-02-22 Test use of mavlink for feedback (not working so far)
    [GroundUnit.ino]
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2015-02-22 Correct missing variable and euclidian division instead of float
    [motorJoy.py]
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2015-02-23 Correct a stupid bug...
    [joystick.py]
2015-02-23 Correct a bug: pressure measurement was listened from ground station instead of embedded device. When changed, the connection to ground station was frozen, so I had to listen to heartbeat
    [motorJoy.py]
2015-02-23 Add heartbeat Correct bug in udp address Add a few protection in case of wrong message
    [motorJoy.py]
2015-02-23 Correct offset and its initial value
    [GroundUnit.ino]
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2015-02-24 Return back to MPU6050 library as getMotion9 is not working and getMag is not in MPU0150 library Works very well!
    [MPU9150_MS5611_IMU.ino]
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2015-03-05 Several changes at once... Add velocity field (wrong, corresponding to x kite axis only) Consider button down event to be able to count increments Factorize the code dealing with increments Saturate 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
    [GroundUnit.ino, motorJoy.py]
2015-03-05 Correct bug (list substration not supported)
    [motorJoy.py]
2015-03-06 automatic IP address Correct a bug when reading feedback Correct a bug on gain tuning (in OL mode instead of AUTO) Correct a bug on increment (counted when pressing and releasing button)
    [motorJoy.py]
2015-03-07 Add handle and "compass" used to measure distance
    [compass.scad, handle.scad]
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2015-03-26 Add a bar mount support
    [bar_mount.scad]
2015-03-28 Add possibility to use colsons
    [bar_mount.scad]
2015-03-28 New iterations
    [bar_mount_reduced.scad]
2015-03-31 Add a few comments
    [bar_mount_reduced.scad]
2015-03-31 Add some pieces to be laser cut to make a support for potentiometer
    [potentiometer_support.scad]
2015-03-31 Add a piece to link two potentiometer to make "gimbal measurement"
    [gimbal_connection.scad]
2015-03-31 Increase thickness and project
    [potentiometer_support.scad]
2015-03-31 Add groud station 3D
    [ground_station.scad]
2015-04-01 Add a piece to support embedded sensor, battery, and RF module
    [embedded_support.scad]
2015-04-01 Reduce space around potentiomètre Add a third layer
    [potentiometer_support.scad]
2015-04-01 Adapt piece to 3D printing Cut piece in two parts to be joined Avoid "echafaudage" Sligtly increase hole for potentiometer
    [gimbal_connection.scad]
2015-04-01 Save basic ring for the bar sensor
    [ring.scad]
2015-04-02 Adapt piece to 3D printing to avoid added material Change to be able to enclose three layers of wood instead of one
    [bar_mount_reduced.scad]
2015-04-02 Add tender (taken from mobile_support.scad)
    [tender.scad]
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2015-06-10 Support for kite bar unit 2
    [line_support.scad]
2015-06-11 Save the (old) work in progress
    [compass.scad, tender.scad]
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2015-07-03 Increase arm length to go on kite bar with longer trim. change diameter to fit to potentiometer
    [compass.scad]
2015-07-03 Do not put the battery and arduino on this part anymore, put on one of the two arm (to be done)
    [line_support.scad]
2015-07-03 Create a support for component to be integrated in waterproof pocket
    [pocket_IMU_sensor.scad]
2015-07-03 Integrate component on the arm of the kite bar sensor
    [arduino_footprint.scad, battery_footprint.scad, support_arm.scad]
2015-07-03 add a protection to avoid to break potentiometer connection
    [potentiometer_support.scad]
2015-07-03 Add minkowski sum to get rounded corners
    [support_arm.scad]
2015-07-14 Reorganize files
    [bar_mount.scad, bar_mount_reduced.scad, compass.scad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]
2015-07-14 Manage obsolete files
    [mobile_support.scad, support.dxf]
2015-07-14 First commit (based on photograph, with a few modifications)
    [load_cell.fzz]
2015-07-14 Add connection with arduino (warning! file is zipped! It should not have been commited as this. Unzip to make a diff
    [load_cell.fzz]
2015-07-23 Correct problem with IsUpdated: it is reset only if value is read. Reduce frequency of order to avoir overwhelming arduino Set feedback rate (now that it is corrected)
    [GroundUnit.ino, motorJoy.py]
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2015-07-24 Correct a bug with saturation which were not properly applied
    [GroundUnit.ino]
2015-07-24 Multiply arbitrary by a factor to increase range and reach saturation even with static error
    [GroundUnit.ino]
2015-08-31 Add text files for load cell parts (taken from ~/.config/Fritzing/fzz)
    [load_cell.fz]
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2015-12-19 First commit of prototype for ring encoder
    [ring_encoder.scad]
2016-01-02 Increase spacing between wheel and support
    [ring_encoder.scad]
2016-01-10 Correct bug in weight torque Add tuning of parameters
2016-01-16 Correct initial value Add time and line tension in output values
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2016-06-20 Add power consumption. Correct effective speed when saturated by ground.
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2020-02-02 Do not display when invalid (-1 is often returned by some components, maybe slightly damaged)
    [HX711_LoadCell.ino]
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2020-02-15 Version testée ce jour : fonctionne correctement !
    [A_RCReceiver.h, PechDavid.ino]
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2021-04-05 rename file to avoid warning on macos/windows
    Warning is:
    warning: the following paths have collided (e.g. case-sensitive paths
    on a case-insensitive filesystem) and only one from the same
    colliding group is in the working tree:
    'ObjectTracking/test/DisplayIPVideoStream.py'
    'ObjectTracking/test/displayIPVideoStream.py'
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2021-11-03 Add slewrate and tune PID to avoid loss of control Format serial output to use serial plotter
    [AK60-6.ino]
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

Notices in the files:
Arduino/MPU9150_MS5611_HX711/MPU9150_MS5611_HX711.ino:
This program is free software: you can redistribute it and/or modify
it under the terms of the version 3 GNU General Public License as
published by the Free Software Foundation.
